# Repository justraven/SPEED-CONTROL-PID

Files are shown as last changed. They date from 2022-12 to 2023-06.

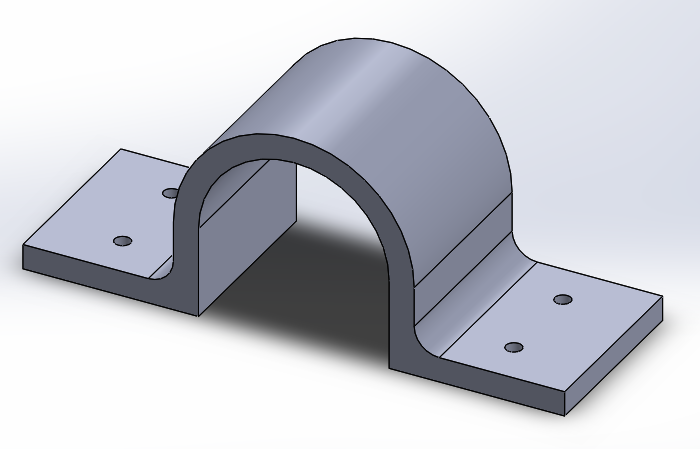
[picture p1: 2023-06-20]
3D Case Design/Desain Mekanik Kendali Motor DC/holder motor dc.PNG

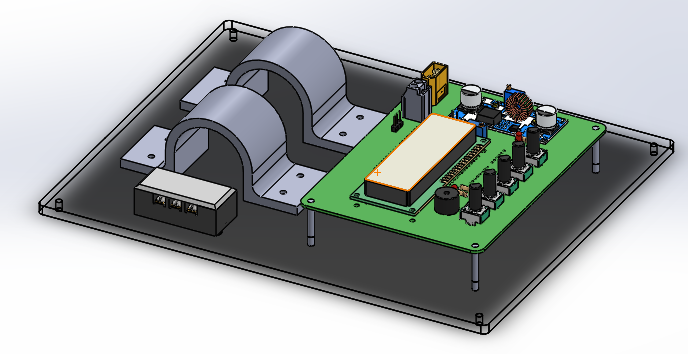
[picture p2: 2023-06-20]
3D Case Design/Desain Mekanik Kendali Motor DC/Desain Mekanik V2 Trimetric.PNG

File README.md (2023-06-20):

# MOTOR DC SPEED CONTROL

Implementing PID control to regulate the speed of a DC motor.

## File Structure
```
📦CODE
 ┣ 📂lib
 ┃ ┣ 📂parsing
 ┃ ┃ ┗ 📜parsing.h
 ┣ 📂src
 ┃ ┗ 📜main.cpp
 📦GUI
 ┣ 📂LABVIEW
 ┃ ┣ 📜block_diagram.pdf
 ┃ ┣ 📜block_diagram_2.pdf
 ┃ ┣ 📜block_diagram_3.pdf
 ┃ ┣ 📜front_panel.pdf
 ┃ ┣ 📜front_panel_2.pdf
 ┃ ┣ 📜front_panel_3.pdf
 ┃ ┣ 📜GUI.vi
 ┃ ┣ 📜GUI_SubVi.vi
 ┃ ┣ 📜PID.txt
 ┃ ┣ 📜PID_2.txt
 ┃ ┣ 📜PID_3.txt
 ┃ ┗ 📜TEST.txt
 ┗ 📂LABVIEW LEGACY
 ┃ ┣ 📂GUI v2
 ┃ ┃ ┗ 📜GUI.vi
 ┃ ┣ 📂GUI v2.1
 ┃ ┃ ┗ 📜GUI.vi
 ┃ ┗ 📜GUI.vi
📦3D Case Design
 ┗ 📂Desain Mekanik Kendali Motor DC
 ┃ ┣ 📜Alas untuk Motor DC.DXF
 ┃ ┣ 📜Alas untuk Motor DC.SLDPRT
 ┃ ┣ 📜Couple Motor.jpeg
 ┃ ┣ 📜Desain Mekanik V1 Atas.PNG
 ┃ ┣ 📜Desain Mekanik V1 Depan.PNG
 ┃ ┣ 📜Desain Mekanik V1 Trimetric kiri.PNG
 ┃ ┣ 📜Desain Mekanik V1 Trimetric.PNG
 ┃ ┣ 📜Desain Mekanik V2 Atas.PNG
 ┃ ┣ 📜Desain Mekanik V2 Trimetric.PNG
 ┃ ┣ 📜Desain Mekanik V3 Atas.PNG
 ┃ ┣ 📜Desain Mekanik V3 Trimetric.PNG
 ┃ ┣ 📜holder motor dc.PNG
 ┃ ┣ 📜Holder Motor DC.SLDPRT
 ┃ ┣ 📜Holder Motor DC.STL
 ┃ ┣ 📜Kendali Motor DC.SLDASM
 ┃ ┣ 📜motor masuk holder.jpeg
 ┃ ┣ 📜Spacer.SLDPRT
 ┃ ┣ 📜SPEED CONTROL MOTOR DC.SLDASM
 ┃ ┣ 📜SPEED_CONTROL_2.step
 ┃ ┣ 📜SPEED_CONTROL_NEW.step
 ┃ ┗ 📜Terminal block TB-1503.SLDASM
 ```
 
## Software Used
- Vscode (with platformio extension)
- LabVIEW (for GUI, I use LabView 21)
- KiCad (I use ver 6.0.10)
- SolidWorks (for 3D modeling)

## Developed by
- Alim Satria [@justraven](https://github.com/justraven) (PCB Design, Firmware)
- Ilham Dwi Cahyo [@ilhamdwi754](https://github.com/ilhamdwi754) (3D Design)

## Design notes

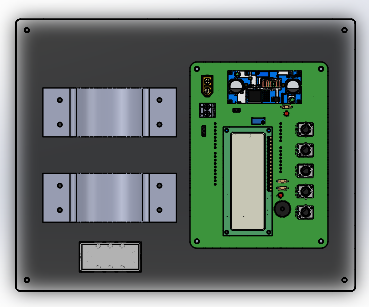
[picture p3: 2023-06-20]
3D Case Design/Desain Mekanik Kendali Motor DC/Desain Mekanik V2 Atas.PNG

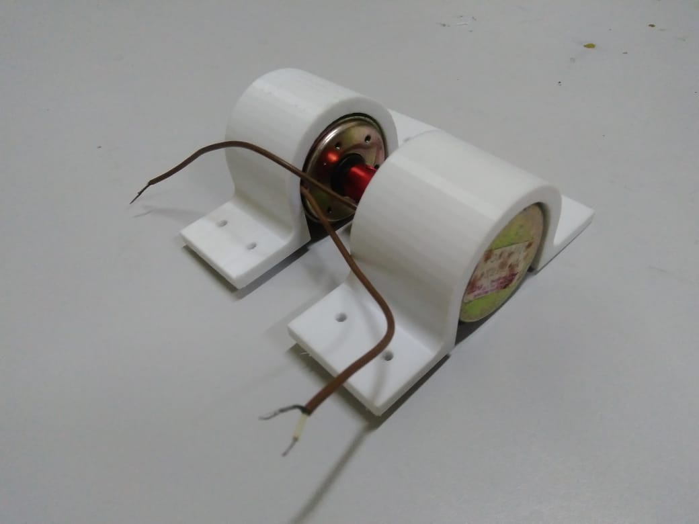
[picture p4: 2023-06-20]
3D Case Design/Desain Mekanik Kendali Motor DC/motor masuk holder.jpeg

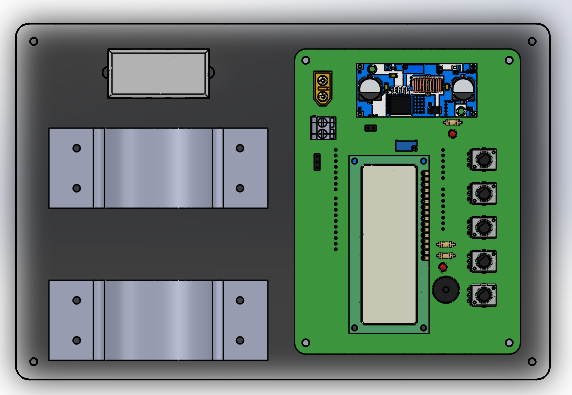
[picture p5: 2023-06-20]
3D Case Design/Desain Mekanik Kendali Motor DC/Desain Mekanik V3 Atas.PNG

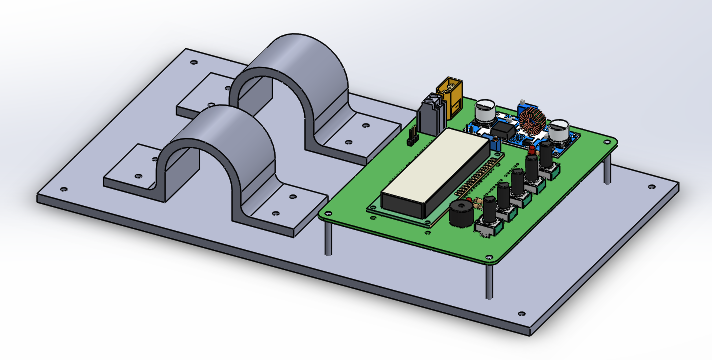
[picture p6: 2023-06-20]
3D Case Design/Desain Mekanik Kendali Motor DC/Desain Mekanik V1 Trimetric.PNG

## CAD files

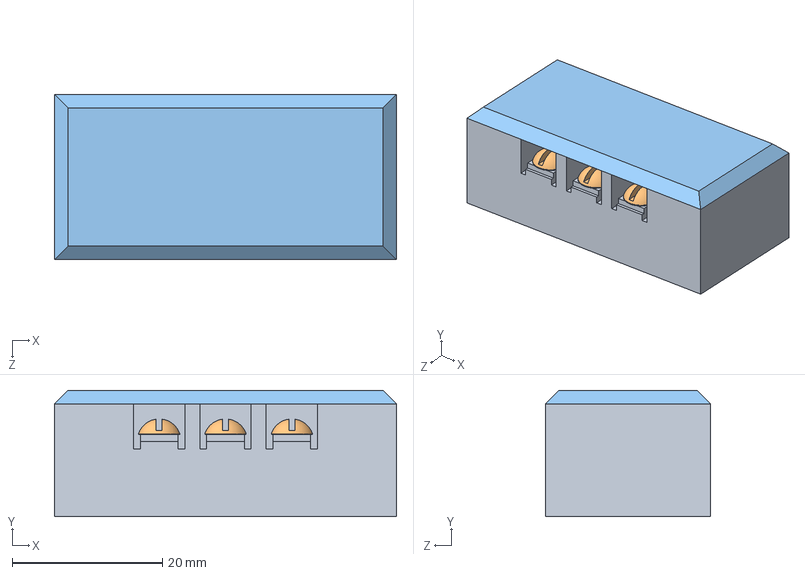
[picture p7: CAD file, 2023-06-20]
3D Case Design/Desain Mekanik Kendali Motor DC/Terminal block TB-1503.SLDASM
45.5 x 16.8 x 22.0 mm
_X2_0414043504420430043B044C_X0_1
_X2_04120438043D0442_X0_ A.M3-6gx3 _X2_0413041E04210422_X0_ 17473-80 x 6
_X2_0414043504420430043B044C_X0_2

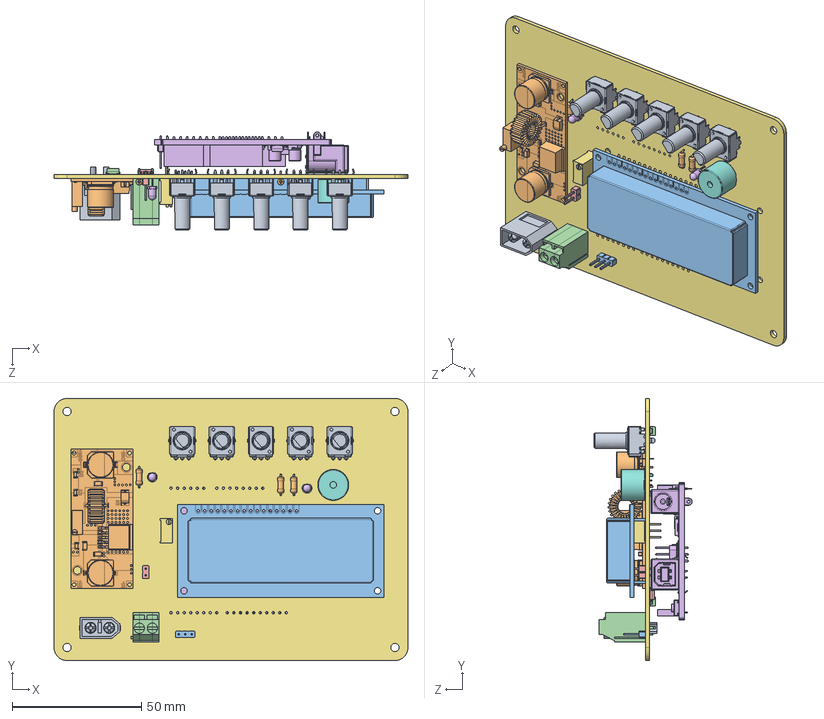
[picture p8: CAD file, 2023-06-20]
3D Case Design/Desain Mekanik Kendali Motor DC/SPEED CONTROL MOTOR DC.SLDASM
137.2 x 101.6 x 38.1 mm
_autosave-SPEED_CONTROL PCB

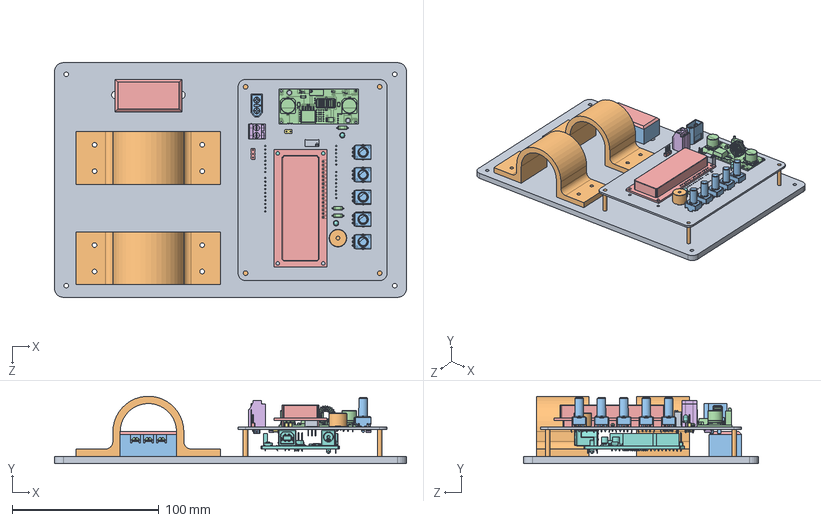
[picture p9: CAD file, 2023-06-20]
3D Case Design/Desain Mekanik Kendali Motor DC/Kendali Motor DC.SLDASM
240.0 x 45.9 x 160.0 mm
Alas untuk Motor DC
Holder Motor DC x 2
_autosave-SPEED_CONTROL PCB
Spacer x 4
_X2_0414043504420430043B044C_X0_1
_X2_04120438043D0442_X0_ A.M3-6gx3 _X2_0413041E04210422_X0_ 17473-80 x 6
_X2_0414043504420430043B044C_X0_2

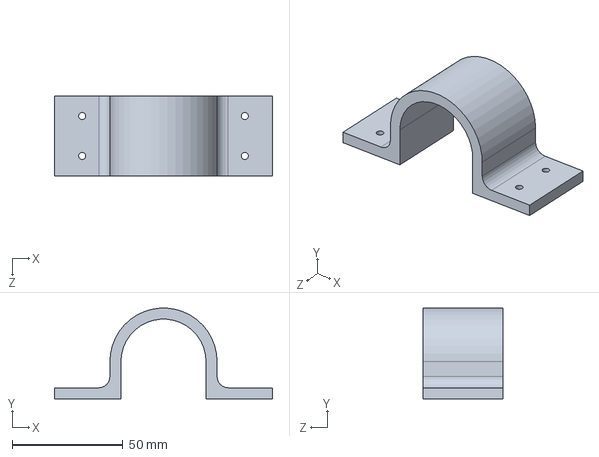
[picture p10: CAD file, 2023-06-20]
3D Case Design/Desain Mekanik Kendali Motor DC/Holder Motor DC.SLDPRT
98.4 x 40.9 x 36.0 mm

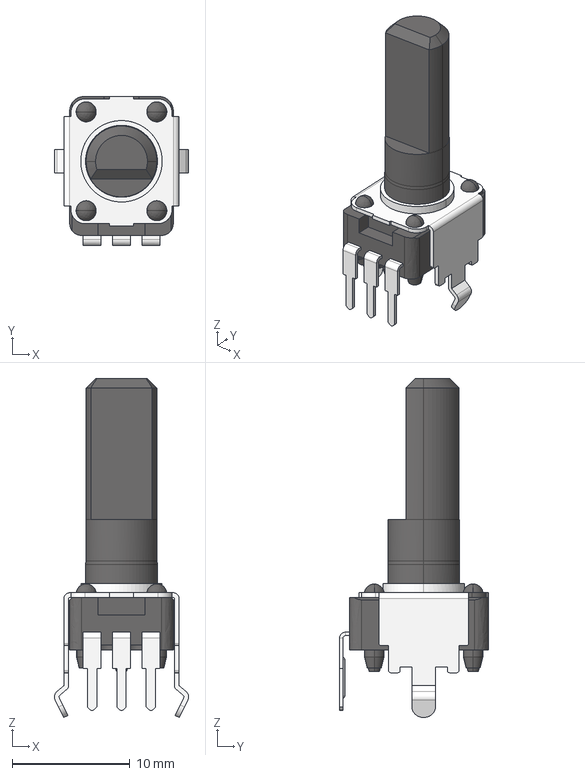
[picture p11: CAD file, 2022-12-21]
PCB DESIGN/SPEED_CONTROL/SPEED_CONTROL/3D MODEL/RK09K1130AH1.STEP
11.4 x 12.7 x 28.8 mm

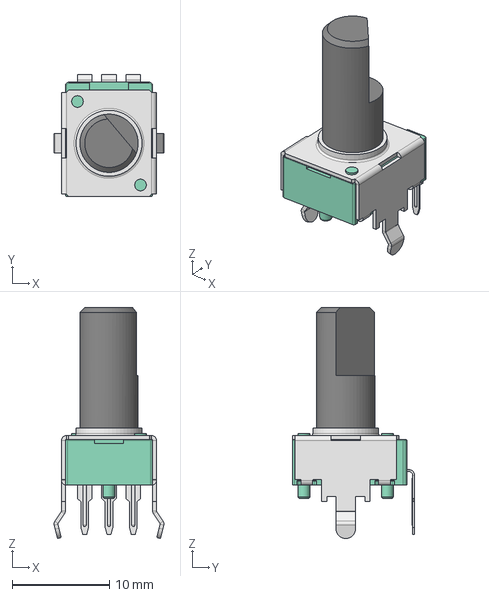
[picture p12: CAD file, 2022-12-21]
PCB DESIGN/SPEED_CONTROL/SPEED_CONTROL/3D MODEL/R-0904N-L-20F-green.step
11.3 x 12.6 x 23.8 mm

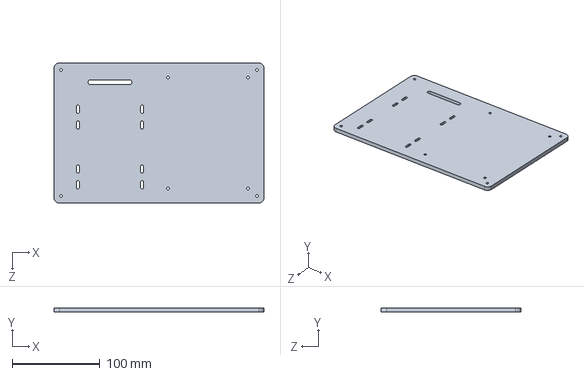
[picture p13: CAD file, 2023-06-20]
3D Case Design/Desain Mekanik Kendali Motor DC/Alas untuk Motor DC.SLDPRT
240.0 x 5.00 x 160.0 mm

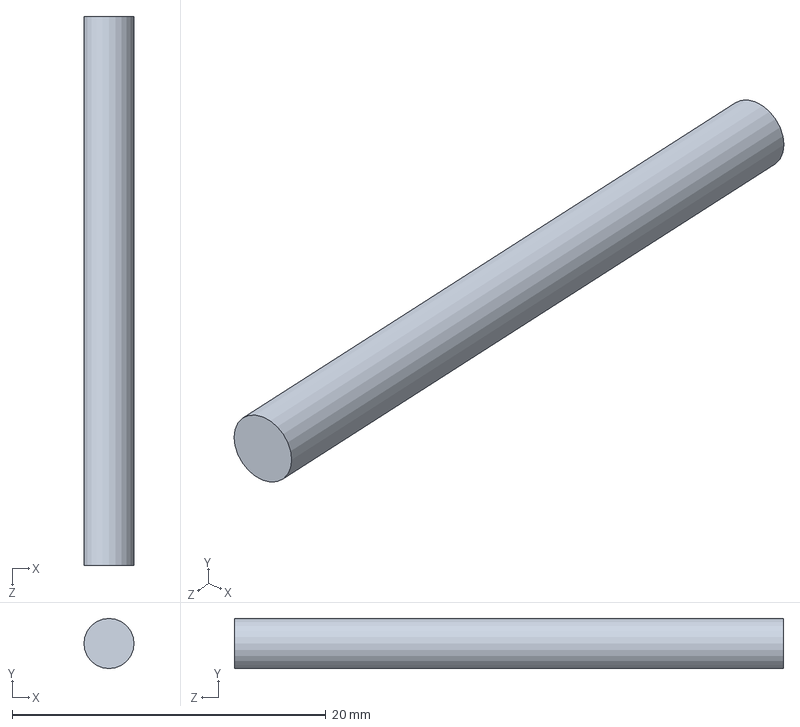
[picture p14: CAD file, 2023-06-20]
3D Case Design/Desain Mekanik Kendali Motor DC/Spacer.SLDPRT
3.20 x 3.20 x 35.0 mm

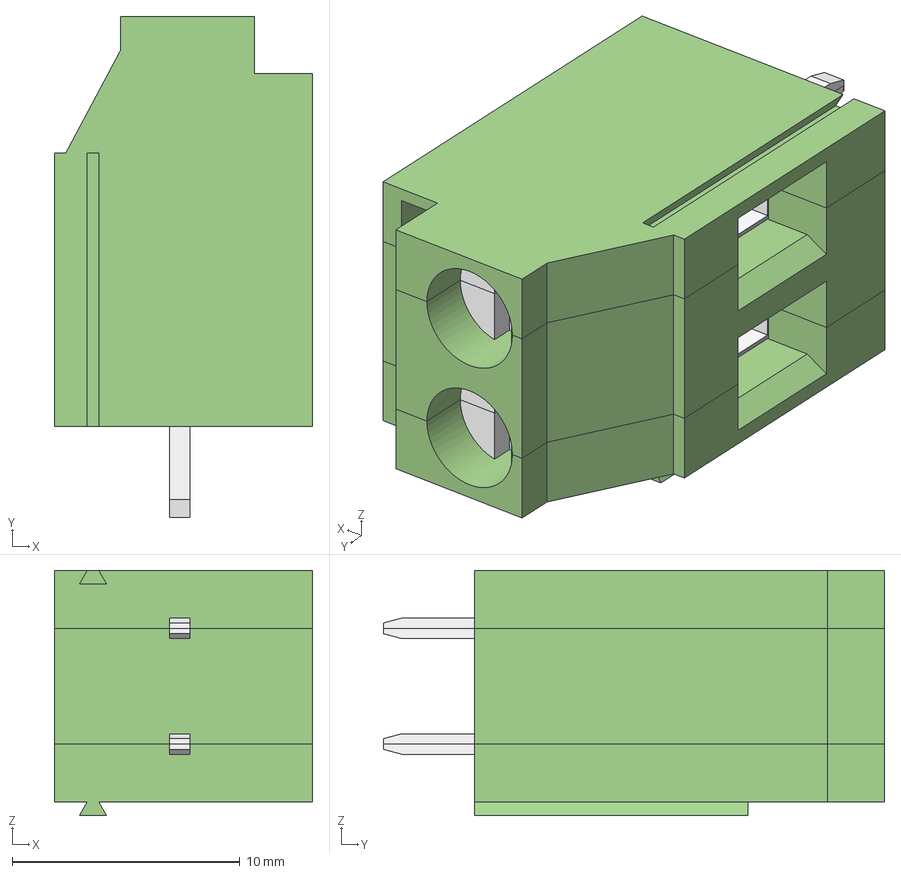
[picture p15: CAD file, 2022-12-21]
PCB DESIGN/SPEED_CONTROL/SPEED_CONTROL/3D MODEL/691236510002 (rev1).stp
11.4 x 22.0 x 10.8 mm
MRT18P5.08V08_SX
MRT18P5.08V08_CNT
MRT18P5.08V08_DX

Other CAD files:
3D Case Design/Desain Mekanik Kendali Motor DC/Alas untuk Motor DC.DXF
3D Case Design/Desain Mekanik Kendali Motor DC/Holder Motor DC.STL

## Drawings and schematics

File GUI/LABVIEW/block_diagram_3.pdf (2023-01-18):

# GUI.vi C:\Users\Alim Satria\Documents\DOKUMEN KULIAH\TKL FMZ\PROJEK\SPEED-CONTROL-PID\

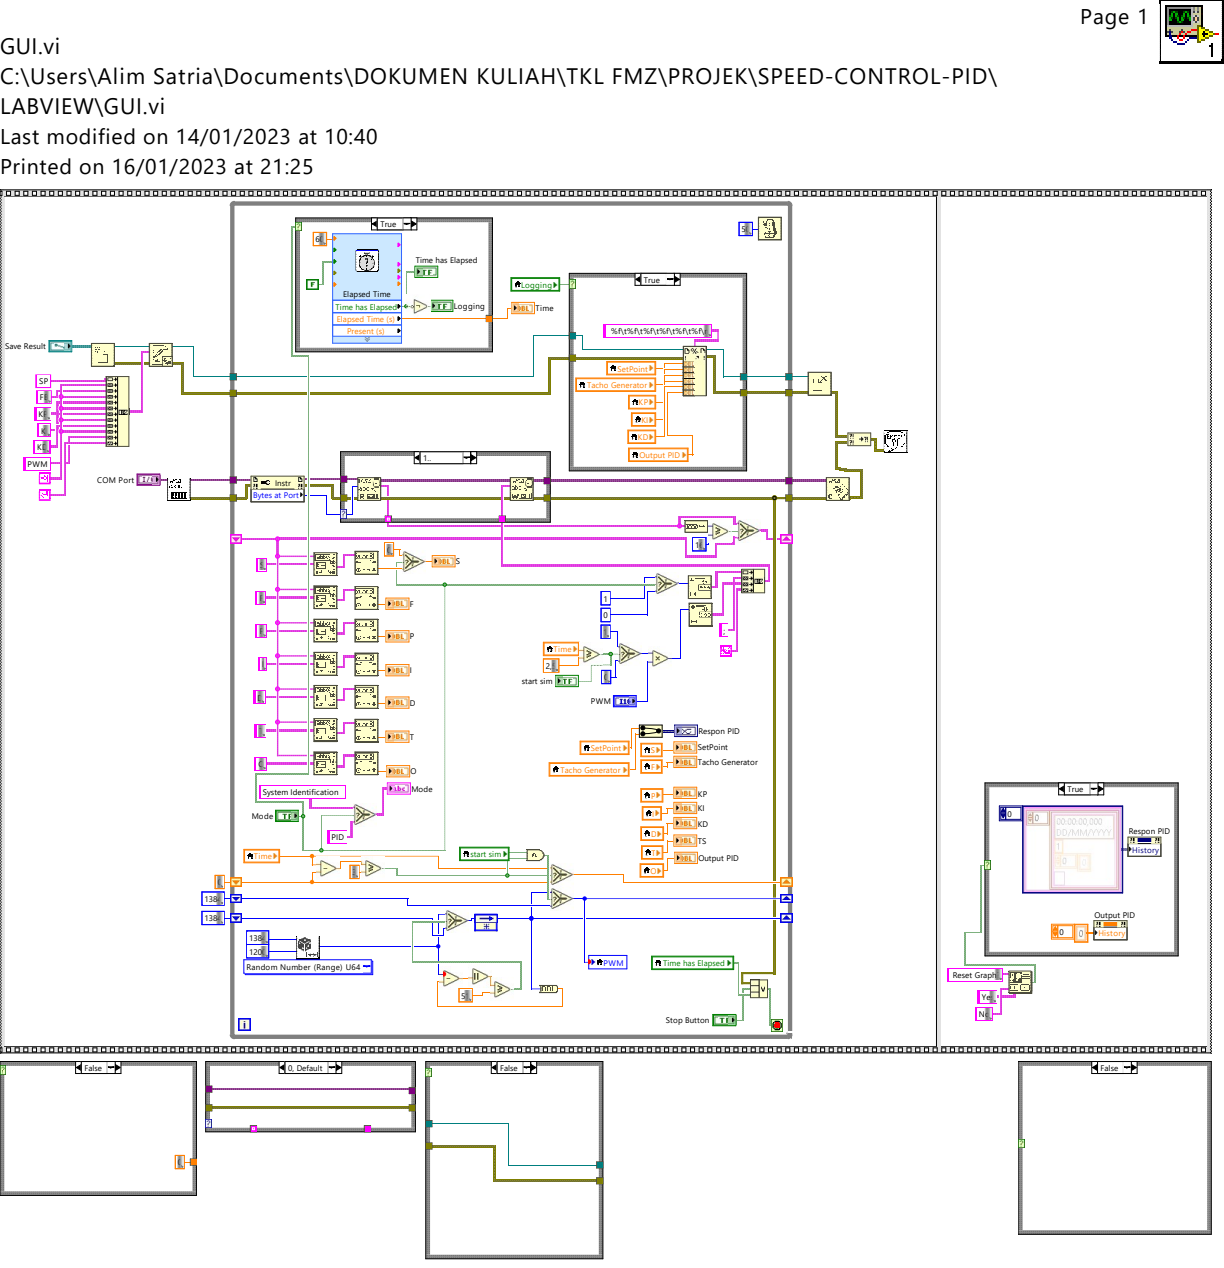
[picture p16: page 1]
Page 1; Instr Bytes at Port; Respon PID; KPKI KD; Stop Button; SetPoint Tacho Generator; Mode; Mode PID; System Identification; ; 1 0 PWM; True Logging; Logging; True; Time; Random Number (Range) U64; 1384 PWM; start sim; PWM; Reset Graph? Yes No; History Respon PID; False; 0, Default

LABVIEW\GUI.vi
Last modified on 14/01/2023 at 10:40
Printed on 16/01/2023 at 21:25

Time has Elapsed

Elapsed Time (s) Present (s) Elapsed Time

SetPoint Tacho Generator %f\t%f\t%f\t%f\t%f\t%f\n KPKI KDOutput PID

COM Port Save Result SP

FB KPKI KD

Time 2,5
SetPoint Tacho Generator Output PID

0 History Output PID
00:00:00,000 DD/MM/YYYY

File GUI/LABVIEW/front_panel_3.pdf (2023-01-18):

## GUI.vi C:\Users\Alim Satria\Documents\DOKUMEN KULIAH\TKL FMZ\PROJEK\SPEED-CONTROL-PID\

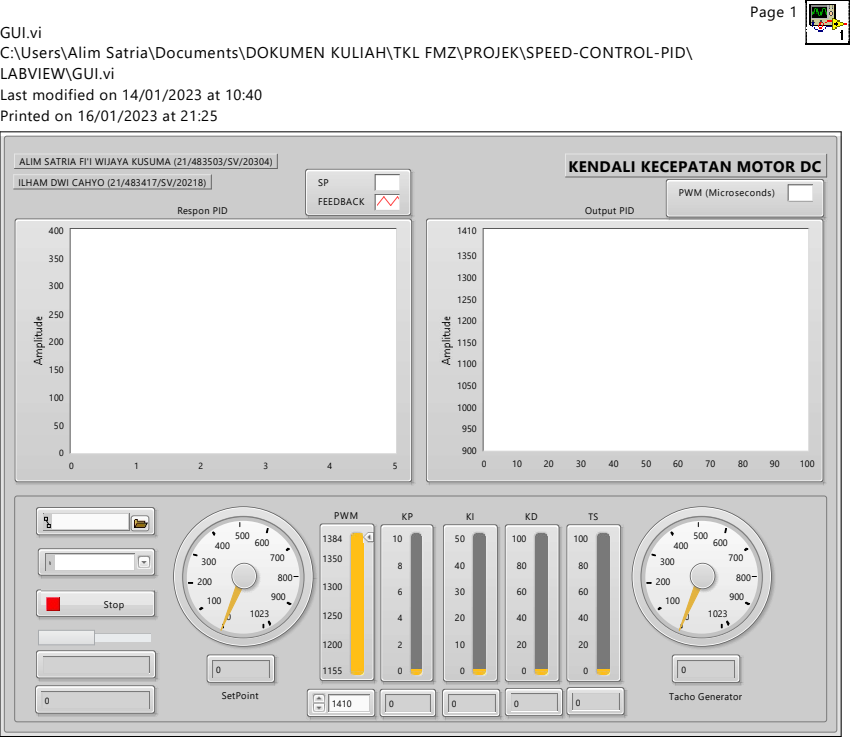
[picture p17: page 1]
Page 1; FEEDBACK; Respon PID; SetPoint; Tacho Generator; PWM (Microseconds); Output PID; Stop; PWM

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

KENDALI KECEPATAN MOTOR DC ALIM SATRIA FI'I WIJAYA KUSUMA (21/483503/SV/20304)
ILHAM DWI CAHYO (21/483417/SV/20218)

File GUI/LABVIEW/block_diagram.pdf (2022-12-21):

# GUI.vi C:\Users\Alim Satria\Documents\DOKUMEN KULIAH\TKL FMZ\PROJEK\LABVIEW\GUI.vi

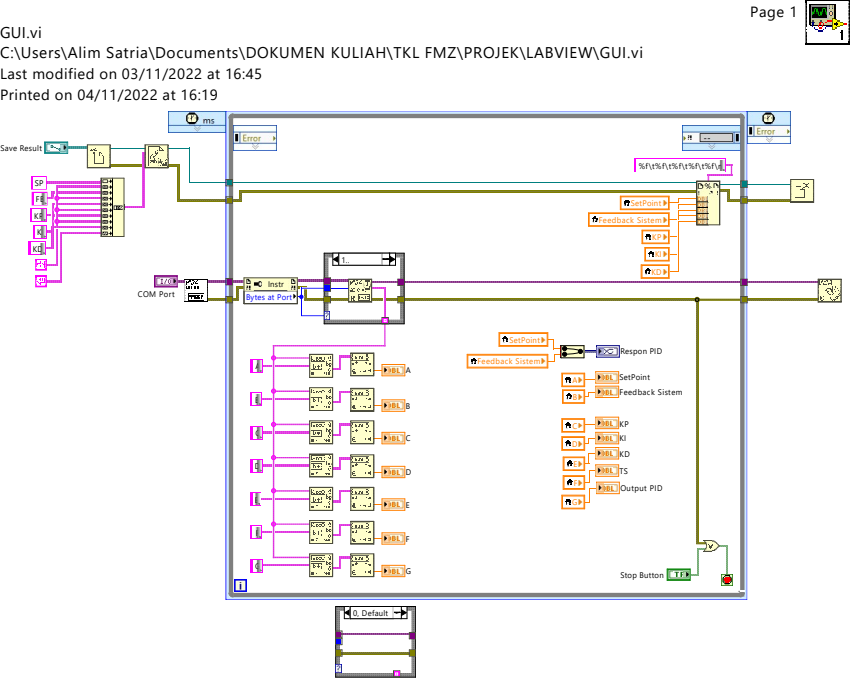
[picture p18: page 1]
Page 1; COM Port; Respon PID; Output PID; KPKI KD; Stop Button; BCD; A BCD; %f\t%f\t%f\t%f\t%f\n KPKI KD; 0, Default

Last modified on 03/11/2022 at 16:45
Printed on 04/11/2022 at 16:19

Save Result SP

FB KPKI KD

SetPoint Feedback Sistem

Instr Bytes at Port

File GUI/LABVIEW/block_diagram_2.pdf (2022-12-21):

# GUI.vi C:\Users\Alim Satria\Documents\DOKUMEN KULIAH\TKL FMZ\PROJEK\LABVIEW\GUI.vi

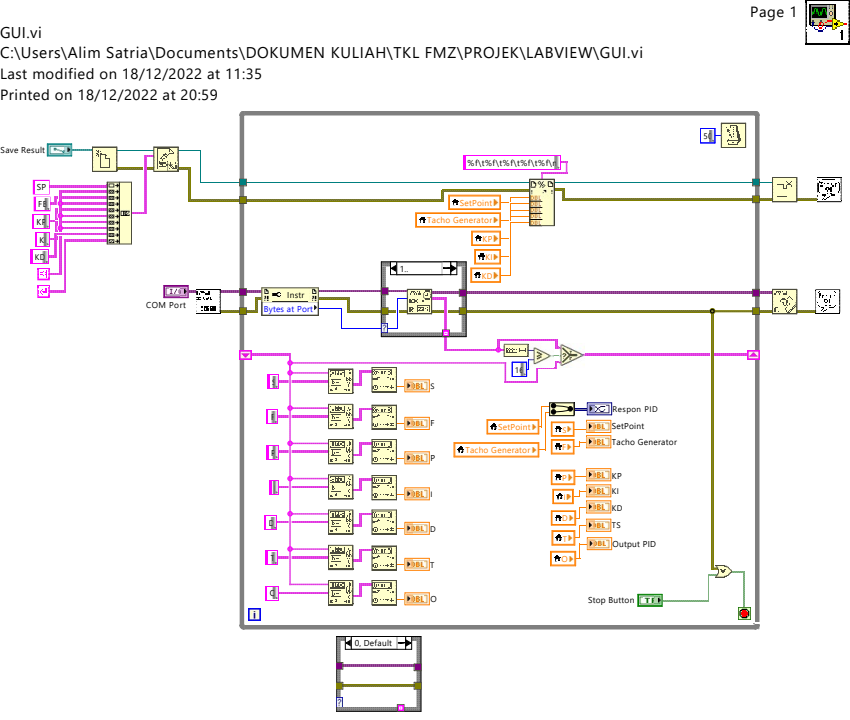
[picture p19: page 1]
Page 1; COM Port; Save Result; Respon PID; SetPoint Tacho Generator; Output PID; KPKI KD; Stop Button; SetPoint; Tacho Generator; %f\t%f\t%f\t%f\t%f\n KPKI KD; 0, Default

Last modified on 18/12/2022 at 11:35
Printed on 18/12/2022 at 20:59

FB KPKI KD

Instr Bytes at Port

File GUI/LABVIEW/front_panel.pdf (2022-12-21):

## GUI.vi C:\Users\Alim Satria\Documents\DOKUMEN KULIAH\TKL FMZ\PROJEK\LABVIEW\GUI.vi

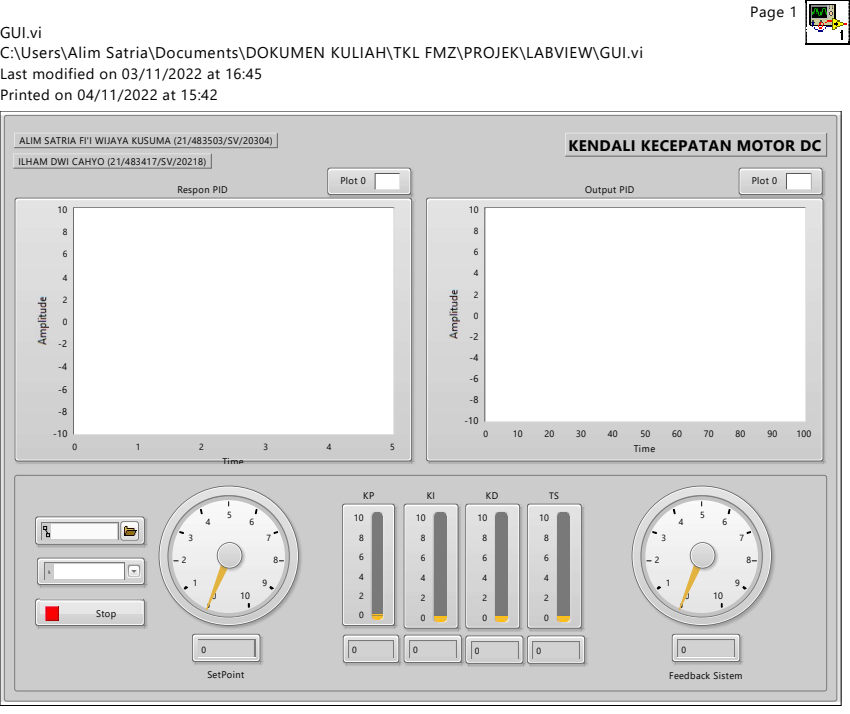
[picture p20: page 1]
Page 1; Time; Plot 0; Respon PID; SetPoint; Feedback Sistem; Output PID; Stop

Last modified on 03/11/2022 at 16:45
Printed on 04/11/2022 at 15:42

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

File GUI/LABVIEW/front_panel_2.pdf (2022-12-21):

## GUI.vi C:\Users\Alim Satria\Documents\DOKUMEN KULIAH\TKL FMZ\PROJEK\LABVIEW\GUI.vi

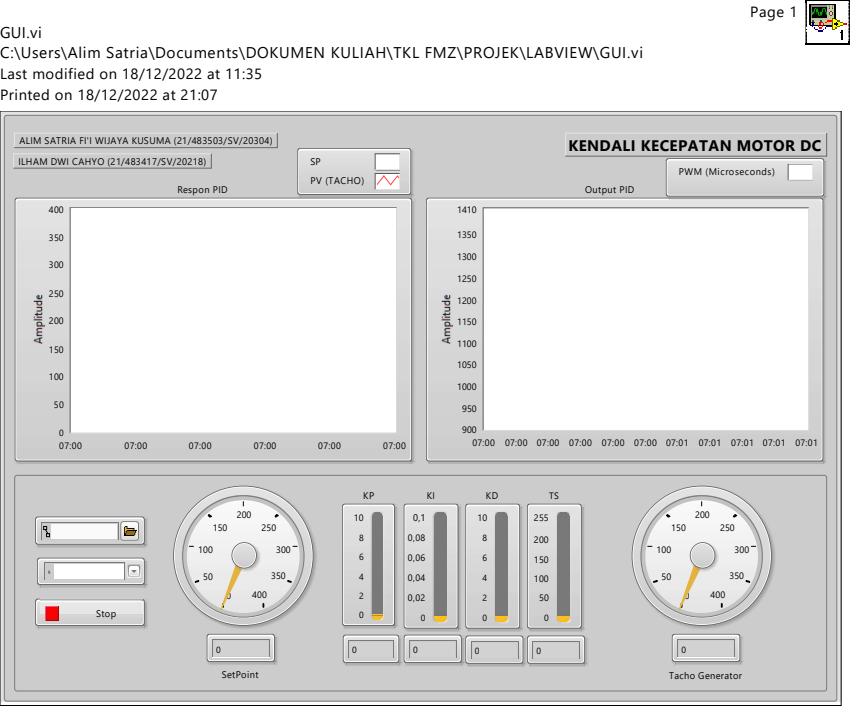
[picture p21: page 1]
Page 1; PV (TACHO); Respon PID; SetPoint; Tacho Generator; PWM (Microseconds); Output PID; Stop

Last modified on 18/12/2022 at 11:35
Printed on 18/12/2022 at 21:07

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

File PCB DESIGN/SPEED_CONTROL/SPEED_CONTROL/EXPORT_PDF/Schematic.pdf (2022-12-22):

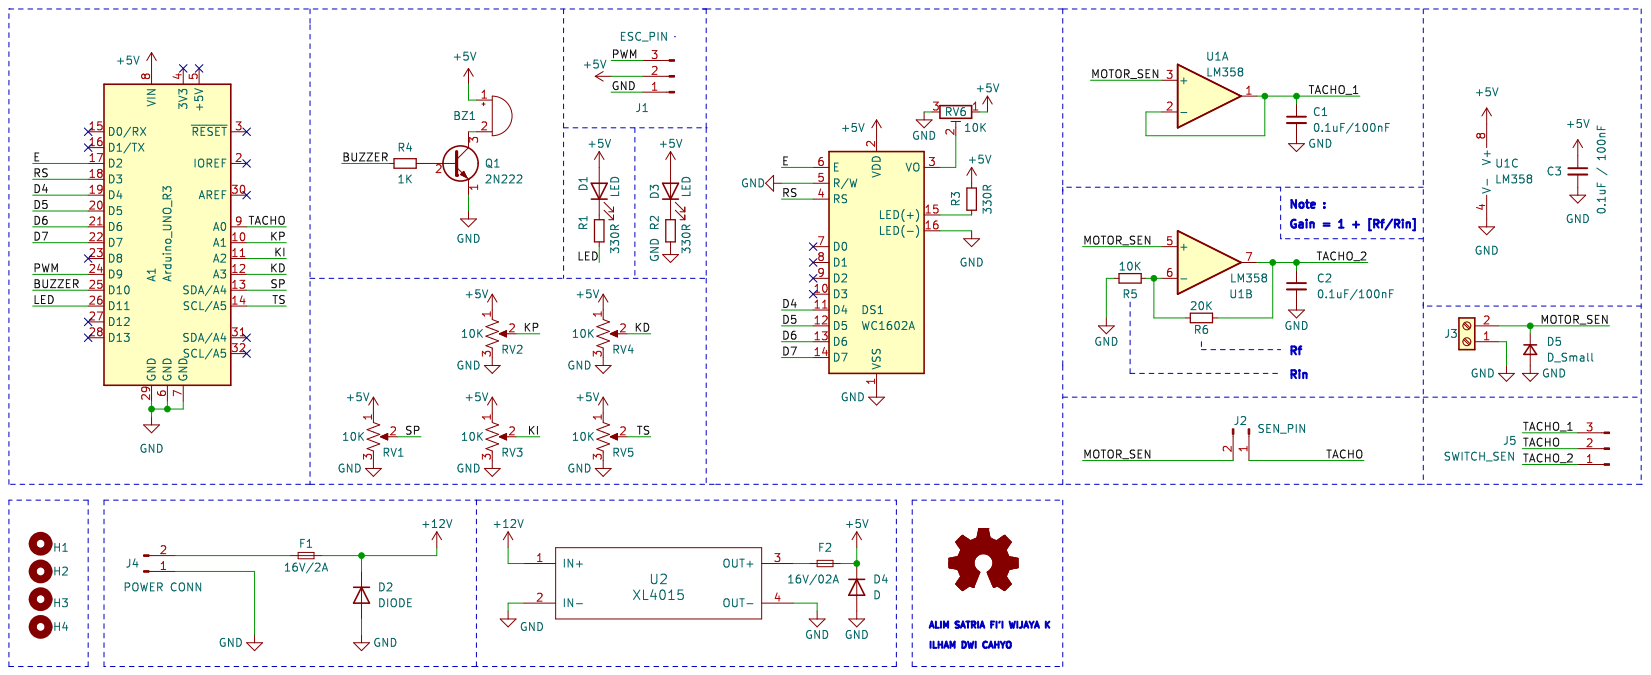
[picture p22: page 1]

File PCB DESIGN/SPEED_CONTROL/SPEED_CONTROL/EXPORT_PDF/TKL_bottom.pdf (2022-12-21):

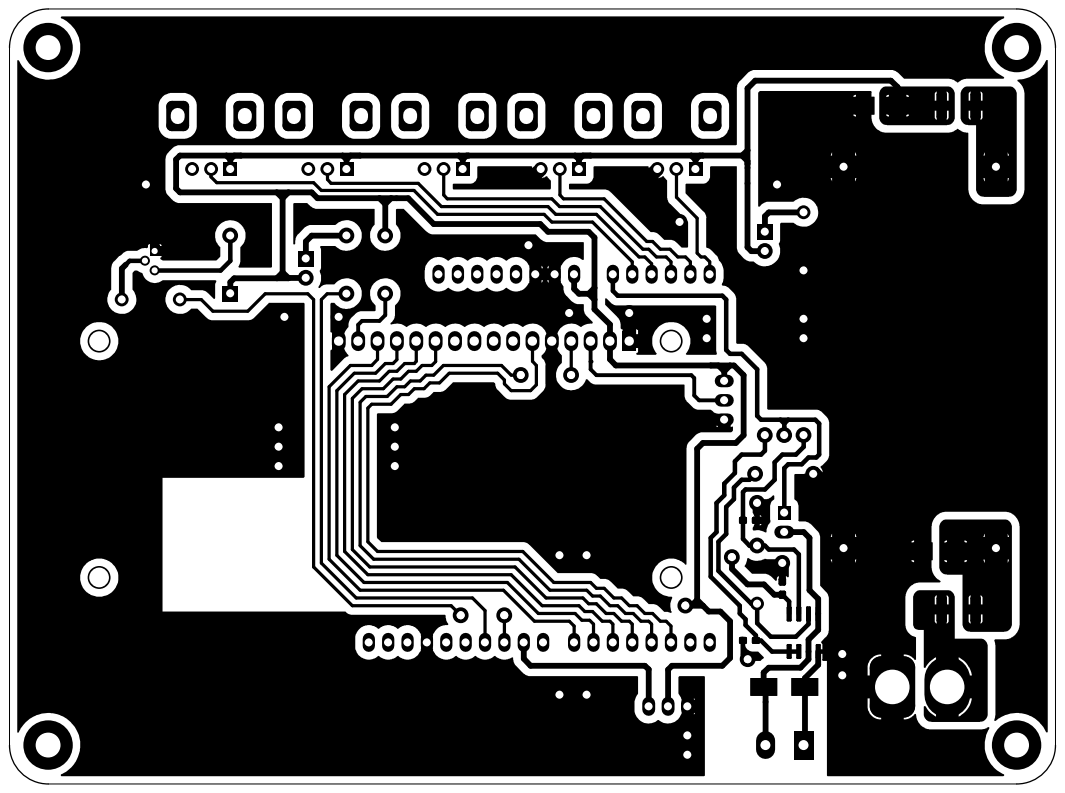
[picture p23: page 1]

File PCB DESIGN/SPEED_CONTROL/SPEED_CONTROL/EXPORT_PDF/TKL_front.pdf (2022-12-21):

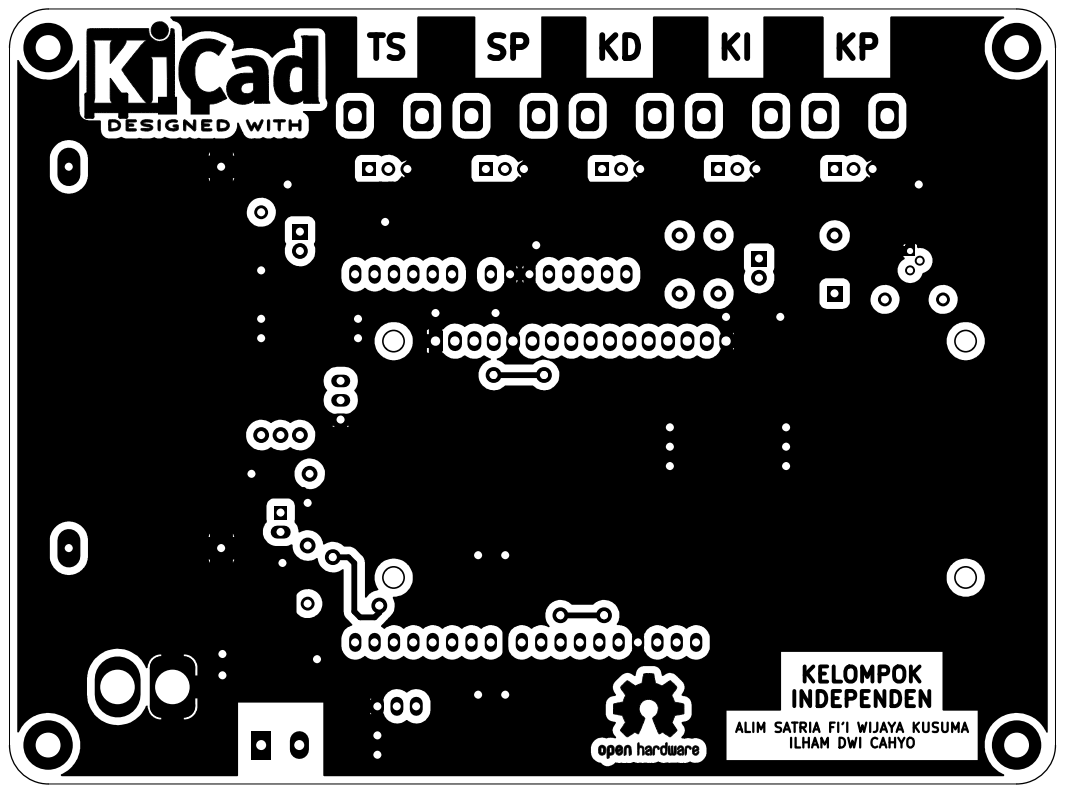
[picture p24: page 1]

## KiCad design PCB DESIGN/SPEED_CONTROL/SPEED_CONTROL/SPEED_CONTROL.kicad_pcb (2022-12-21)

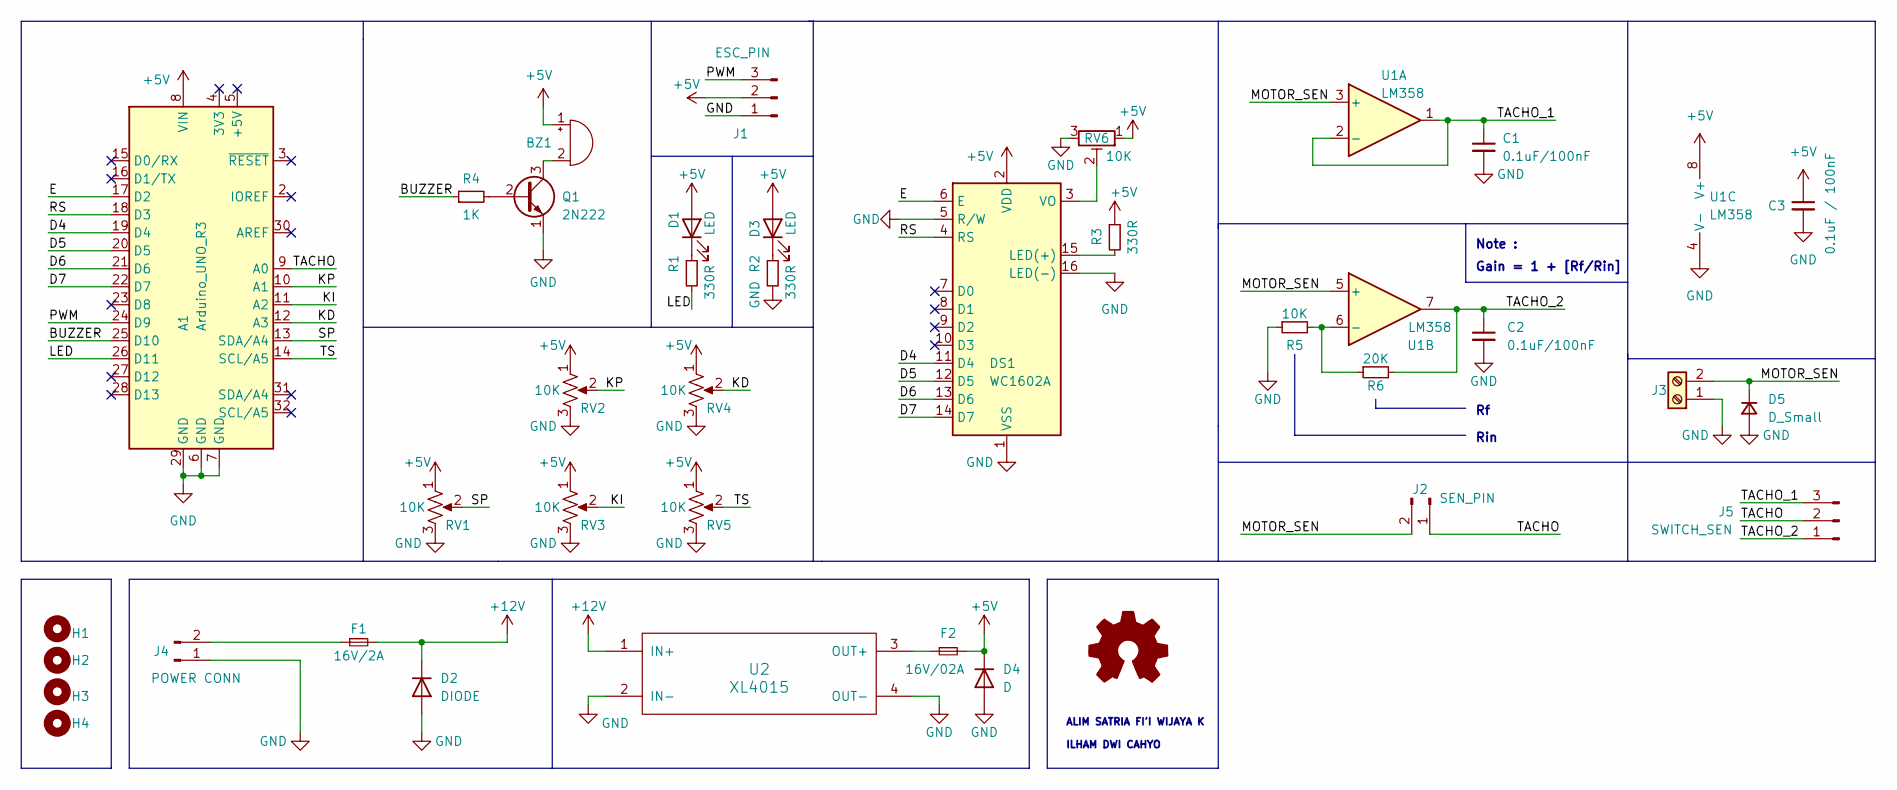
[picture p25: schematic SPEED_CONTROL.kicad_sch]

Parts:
A1: Arduino_UNO_R3
BZ1: Buzzer; MagneticBuzzer_ProSignal_ABI-009-RC
C1, C2: 0.1uF/100nF; C_0603_1608Metric_Pad1.08x0.95mm_HandSolder
C3: 0.1uF / 100nF; C_0603_1608Metric_Pad1.08x0.95mm_HandSolder
D1, D3: LED; LED_D3.0mm
D2: DIODE; D_SMB
D4: D; D_SMB
D5: D_Small; D_SMB_Handsoldering
DS1: WC1602A
F1: 16V/2A; Fuse_1812_4532Metric_Pad1.30x3.40mm_HandSolder
F2: 16V/02A; Fuse_1812_4532Metric_Pad1.30x3.40mm_HandSolder
H1, H2, H3, H4: MountingHole; MountingHole_3.2mm_M3_Pad
J1: ESC_PIN; PinHeader_1x03_P2.54mm_Vertical
J2: SEN_PIN; PinHeader_1x02_P2.54mm_Vertical
J3: Screw_Terminal_01x02; TerminalBlock_RND_205-00001_1x02_P5.00mm_Horizontal
J4: POWER CONN; AMASS_XT60-M_1x02_P7.20mm_Vertical
J5: SWITCH_SEN; PinHeader_1x03_P2.54mm_Vertical
Q1: 2N222; TO-92
R1, R2, R3: 330R; R_Axial_DIN0207_L6.3mm_D2.5mm_P7.62mm_Horizontal
R4: 1K; R_Axial_DIN0207_L6.3mm_D2.5mm_P7.62mm_Horizontal
R5: 10K; R_Axial_DIN0207_L6.3mm_D2.5mm_P7.62mm_Horizontal
R6: 20K; R_Axial_DIN0207_L6.3mm_D2.5mm_P7.62mm_Horizontal
RV1, RV2, RV3, RV4, RV5: 10K; Potentiometer_Alps_RK09K_Single_Vertical
RV6: 10K; Potentiometer_Bourns_3296W_Vertical
U1: LM358; SOIC-8_3.9x4.9mm_P1.27mm
U2: XL4015; XL4015_Converter

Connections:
+5V: A1.8 (VIN), BZ1.1 (-), C3.1, D1.2 (A), D3.2 (A), D4.1 (K), DS1.2 (VDD), F2.2, J1.2, R3.1, RV1.1, RV2.1, RV3.1, RV4.1, RV5.1, RV6.1, U1.8 (V+)
+12V: D2.2 (K), F1.2, U2.1 (IN+)
/BUZZER: A1.25 (D10), R4.1
/D4: A1.19 (D4), DS1.11 (D4)
/D5: A1.20 (D5), DS1.12 (D5)
/D6: A1.21 (D6), DS1.13 (D6)
/D7: A1.22 (D7), DS1.14 (D7)
/E: A1.17 (D2), DS1.6 (E)
/KD: A1.12 (A3), RV4.2
/KI: A1.11 (A2), RV3.2
/KP: A1.10 (A1), RV2.2
/LED: A1.26 (D11), R1.2
/MOTOR_SEN: D5.1 (K), J2.2, J3.2, U1.3 (+), U1.5 (+)
/PWM: A1.24 (D9), J1.3
/RS: A1.18 (D3), DS1.4 (RS)
/SP: A1.13 (SDA/A4), RV1.2
/TACHO: A1.9 (A0), J2.1, J5.2
/TACHO_1: C1.1, J5.3, U1.1, U1.2 (-)
/TACHO_2: C2.1, J5.1, R6.2, U1.7
/TS: A1.14 (SCL/A5), RV5.2
GND: A1.6 (GND), A1.7 (GND), A1.29 (GND), C1.2, C2.2, C3.2, D2.1 (A), D4.2 (A), D5.2 (A), DS1.1 (VSS), DS1.5 (R/W), DS1.16 (LED(-)), J1.1, J3.1, J4.1, Q1.1 (E), R2.2, R5.1, RV1.3, RV2.3, RV3.3, RV4.3, RV5.3, RV6.3, U1.4 (V-), U2.2 (IN-), U2.4 (OUT-)
unnamed: BZ1.2 (+), Q1.3 (C)
unnamed: D1.1 (K), R1.1
unnamed: D3.1 (K), R2.1
unnamed: DS1.3 (VO), RV6.2
unnamed: DS1.15 (LED(+)), R3.2
unnamed: F2.1, U2.3 (OUT+)
unnamed: F1.1, J4.2
unnamed: Q1.2 (B), R4.2
unnamed: R5.2, R6.1, U1.6 (-)

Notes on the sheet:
ALIM SATRIA FI'I WIJAYA K ILHAM DWI CAHYO
Rin
Note :
Gain = 1 + [Rf/Rin]

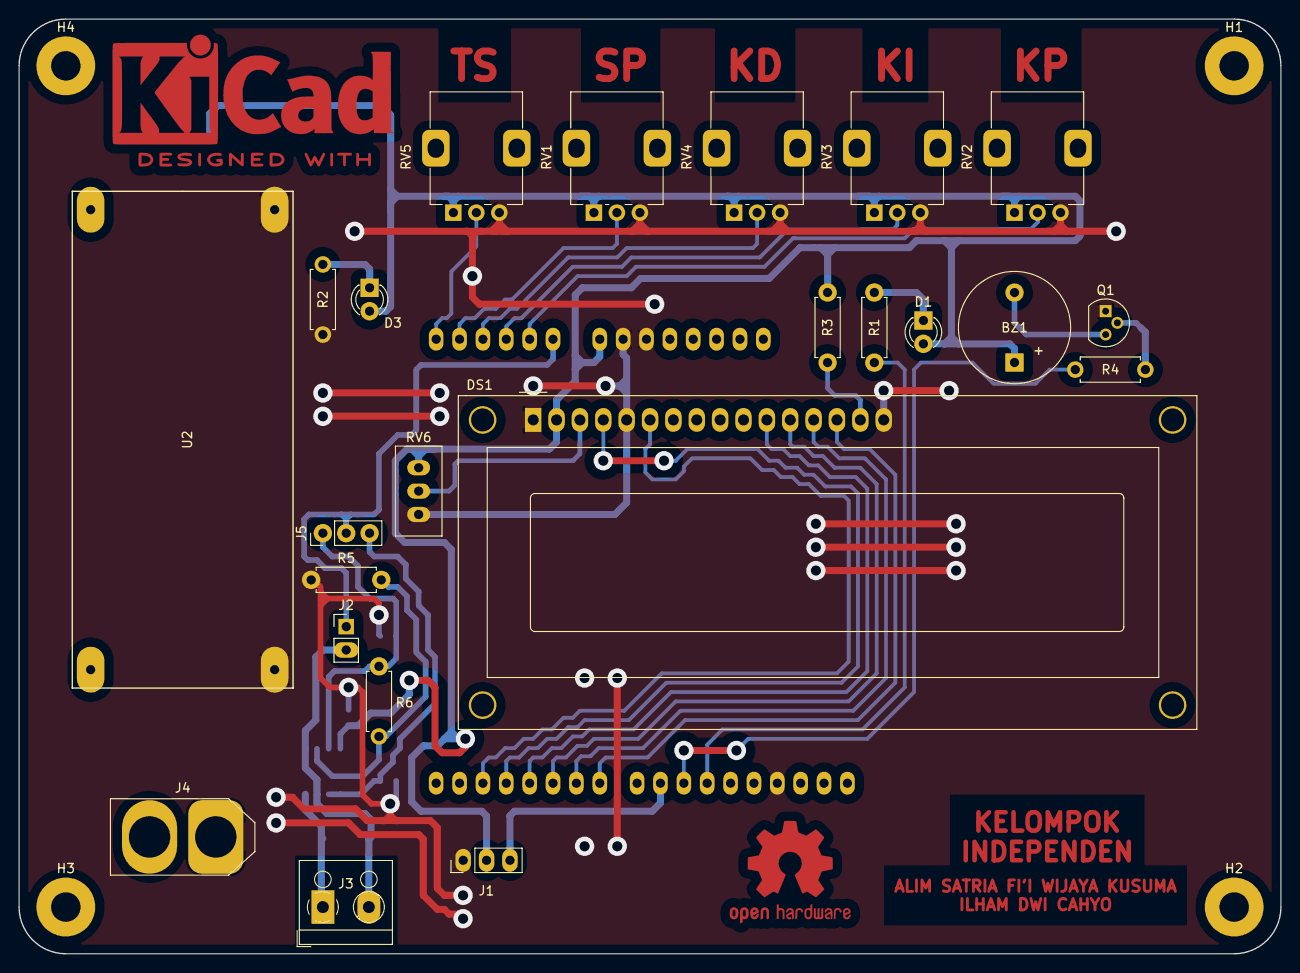
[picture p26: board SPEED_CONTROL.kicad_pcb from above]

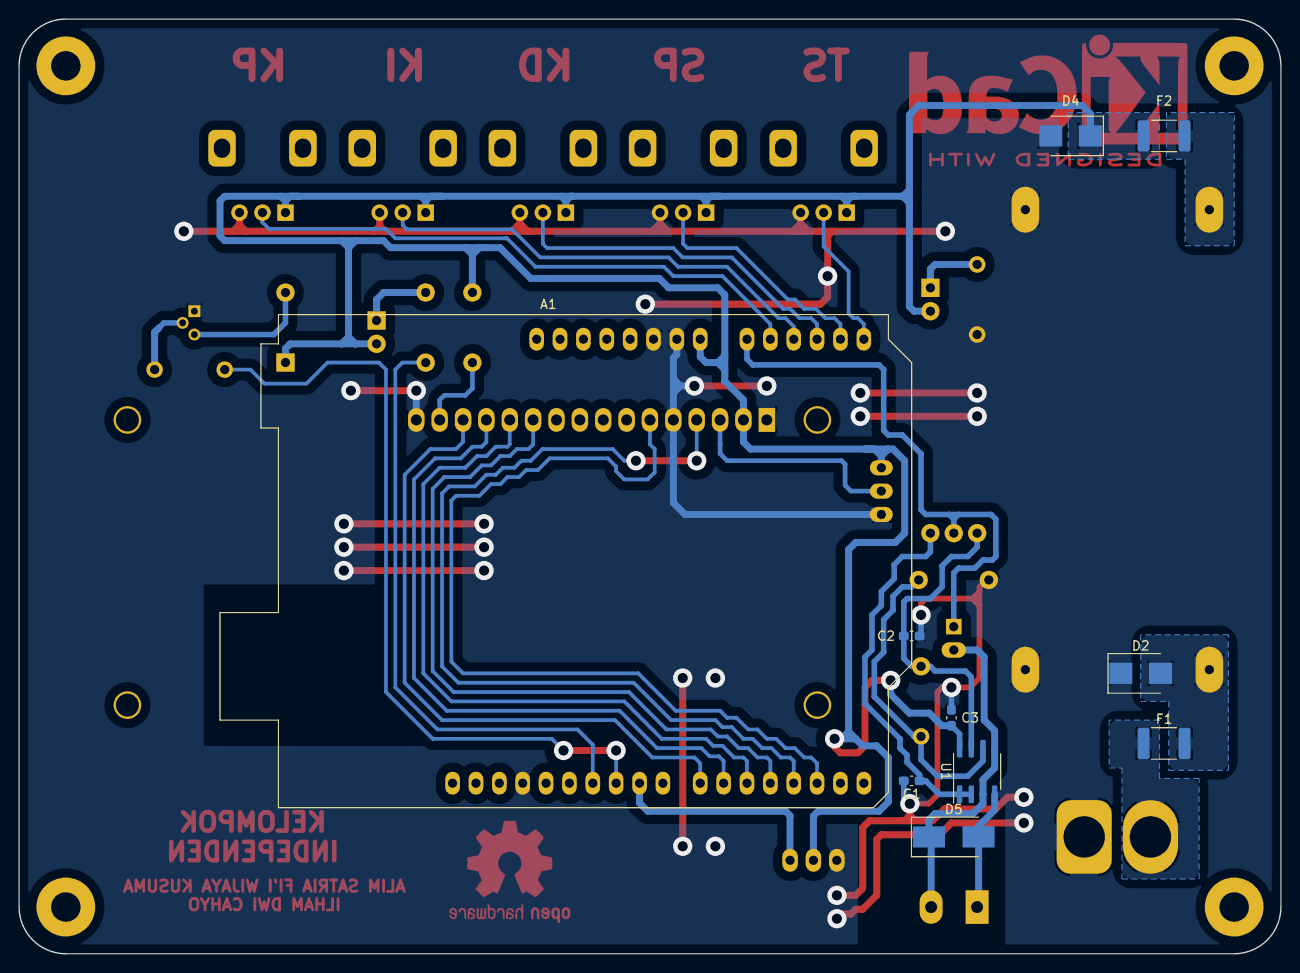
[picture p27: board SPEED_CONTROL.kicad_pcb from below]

Board: 2 copper layers, 137.2 x 101.6 mm, 37 parts (10 on the bottom side), 30 nets.

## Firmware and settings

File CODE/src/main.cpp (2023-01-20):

#include <Arduino.h>

#include <LiquidCrystal.h>
#include <Servo.h>

#include <parsing.h>

#define TACHO_GENERATOR A0

//----- POT PINs -----//
#define KP_PIN A1
#define KI_PIN A2
#define KD_PIN A3
#define SET_POINT_PIN     A4
#define TIME_SAMPLING_PIN A6

//----- INDICATOR -----//
#define BUZZER 10
#define LED 11

//----- LCD PINs -----//
#define RS 3
#define EN 2
#define D4 4
#define D5 5
#define D6 6
#define D7 7

LiquidCrystal lcd(RS,EN,D4,D5,D6,D7);

//----- filter variable -----//
float sum = 0, average = 0;
float averageFilter(uint8_t analogPin,int N);

//----- ESC -----//
Servo esc;
int escValue = 0;

//----- loop time -----//
unsigned long t = 0;
uint8_t timeSampling = 50; //period of loop : 50ms

//----- PID Variable -----//
float KP, KI, KD, KP_, KI_, KD_;
float setPoint, feedback, controlSignal; //velocity is feedback sensor
float error = 0.00, totalError, lastError, deltaError;
float maxControl = 1410;
float minControl = 900;

//----- parsing variable -----//
int mode;
float PWM;

//----- map float -----//
float mapFloat(float x, float inMin, float inMax, float outMin, float outMax){
  return (x - inMin) * (outMax - outMin) / (inMax - inMin) + outMin;
}

void setup() {

  Serial.begin(115200);

  lcd.begin(16,2);
  esc.attach(9);

  pinMode(BUZZER,OUTPUT);
  pinMode(LED,OUTPUT);

  digitalWrite(BUZZER,LOW);
  digitalWrite(LED,HIGH);

  // esc.writeMicroseconds(minControl);
  // delay(1000);
  // esc.writeMicroseconds(maxControl);
  // delay(1000);

}

void loop() {

  if(Serial.available() > 0){

    READ_DATA_UNTIL('\n');
    data.replace(',','.');
    parseString();

    mode           = DATA_STR(0).toInt();
    controlSignal  = DATA_STR(1).toFloat(); 

    Serial.flush();

  }

  if(millis() - t > timeSampling){

    t += timeSampling;

    feedback = averageFilter(TACHO_GENERATOR,200);

    if(mode == 0){

      KP = mapFloat(analogRead(KP_PIN),0,883,0,10);
      KI = mapFloat(analogRead(KI_PIN),0,883,0,100);
      KD = mapFloat(analogRead(KD_PIN),0,883,0,10);

      // KP = 1.529;
      // KI = 0.01619;
      // KD = 0.1829;

      // KP = 1.313;
      // KI = 0.01371;
      // KD = 0.1396;

      // KP = 1.414;
      // KI = 0.0264;
      // KD = 0.08539;


      setPoint = map(analogRead(SET_POINT_PIN),0,883,0,400);

      error = setPoint - feedback;
      totalError += error;

      if (totalError >= maxControl) totalError = maxControl;
      else if (totalError <= minControl) totalError = minControl;

      deltaError = error - lastError;

      KP_ = KP * error;
      KI_ = (KI/1000) * totalError * timeSampling;
      // KI_ = KI * totalError * timeSampling;
      KD_ = (KD / timeSampling) * deltaError;

      controlSignal = KP_ + KI_ + KD_;

      if(controlSignal >= maxControl) controlSignal = maxControl;
      else if(controlSignal <= minControl) controlSignal = minControl;

      esc.writeMicroseconds(controlSignal);

      lastError = error;

    }

    else if (mode == 1){

      if(controlSignal >= maxControl)
        controlSignal = maxControl;
      else if(controlSignal <= minControl)
        controlSignal = minControl;

      esc.writeMicroseconds(controlSignal);      

    }

    String S = String(setPoint);
    String F = String(feedback);
    String P = String(KP);
    String I = String(KI);
    String D = String(KD);
    String T = String(timeSampling);
    String O = String(controlSignal);

    S.replace('.',',');
    F.replace('.',',');
    P.replace('.',',');
    I.replace('.',',');
    D.replace('.',',');
    T.replace('.',',');
    O.replace('.',',');

    Serial.print('S');Serial.print(S);
    Serial.print('F');Serial.print(F);
    Serial.print('P');Serial.print(P);
    Serial.print('I');Serial.print(I);
    Serial.print('D');Serial.print(D);
    Serial.print('T');Serial.print(T);
    Serial.print('O');Serial.println(O);

    lcd.setCursor(0,0);
    lcd.print("SP:");lcd.print(S);
    lcd.setCursor(0,1);
    lcd.print("PV:");lcd.print(F);
    lcd.flush();
    

  }

}

float averageFilter(uint8_t analogPin, int N){

  sum = 0;

  for(int i = 0; i < N; i++)
    sum += analogRead(analogPin);
  
  average = sum / N;

  return average;

}

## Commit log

2022-12-21 add files
    add PCB Design file, code, and GUI program
    [691236510002 (rev1).stp, Projek Kendali Motor DC.kicad_pcb, Projek Kendali Motor DC.kicad_sch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]
2022-12-22 remove some file
    [Projek Kendali Motor DC.kicad_pcb, Projek Kendali Motor DC.kicad_sch]
2022-12-22 add PCB schematic documentation
2023-01-18 add identification system on matlab
    [DATASET.xlsx]
2023-01-20 smoothing signal and add stability
    - Change baud rate to 115200
    - Change moving average filter coefficient to 200
    - Update on LabView Serial Communication
    [main.cpp]
2023-01-31 add 3D model with PCB track
2023-02-02 tyding up folders
    [691236510002 (rev1).stp, DATASET.xlsx, R-0904N-L-20F-green.step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]
2023-06-20 add 3D Model
    [Alas untuk Motor DC.DXF, Alas untuk Motor DC.SLDPRT, Holder Motor DC.SLDPRT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]
